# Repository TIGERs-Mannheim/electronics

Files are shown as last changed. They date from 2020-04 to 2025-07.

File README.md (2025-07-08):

# TIGERs Mannheim Open-Source Electronics

This repository contains electronics for our robots and our base station. There is one folder for each released version.  
Have a look at our [2020 ETDP](https://tigers-mannheim.de/download/tdps/2020_ETDP_TIGERS.pdf) which contains many details about design decisions and lessons learned over the last 10 years.

The following files are present for each release.

### EAGLE
Electronics are designed with [Autodesk EAGLE](https://www.autodesk.com/education/free-software/eagle) which is available for free for students.
This folder contains all schematics (.sch) and board (.brd) files.

### KiCad9
EAGLE files converted to KiCad version 9. Files got only a light cleanup pass.
Note that no PCBs were ever produced using these files. The EAGLE files are still the ground truth.

### PDF
All schematics are also available as PDF files. This makes it easier to view them without a need to install EAGLE.

### CAM
CAM jobs for EAGLE. Used to produce manufacturing data from board files.

### Gerber
Production ready zip packages for all boards. Most PCB production services directly accept gerber files.

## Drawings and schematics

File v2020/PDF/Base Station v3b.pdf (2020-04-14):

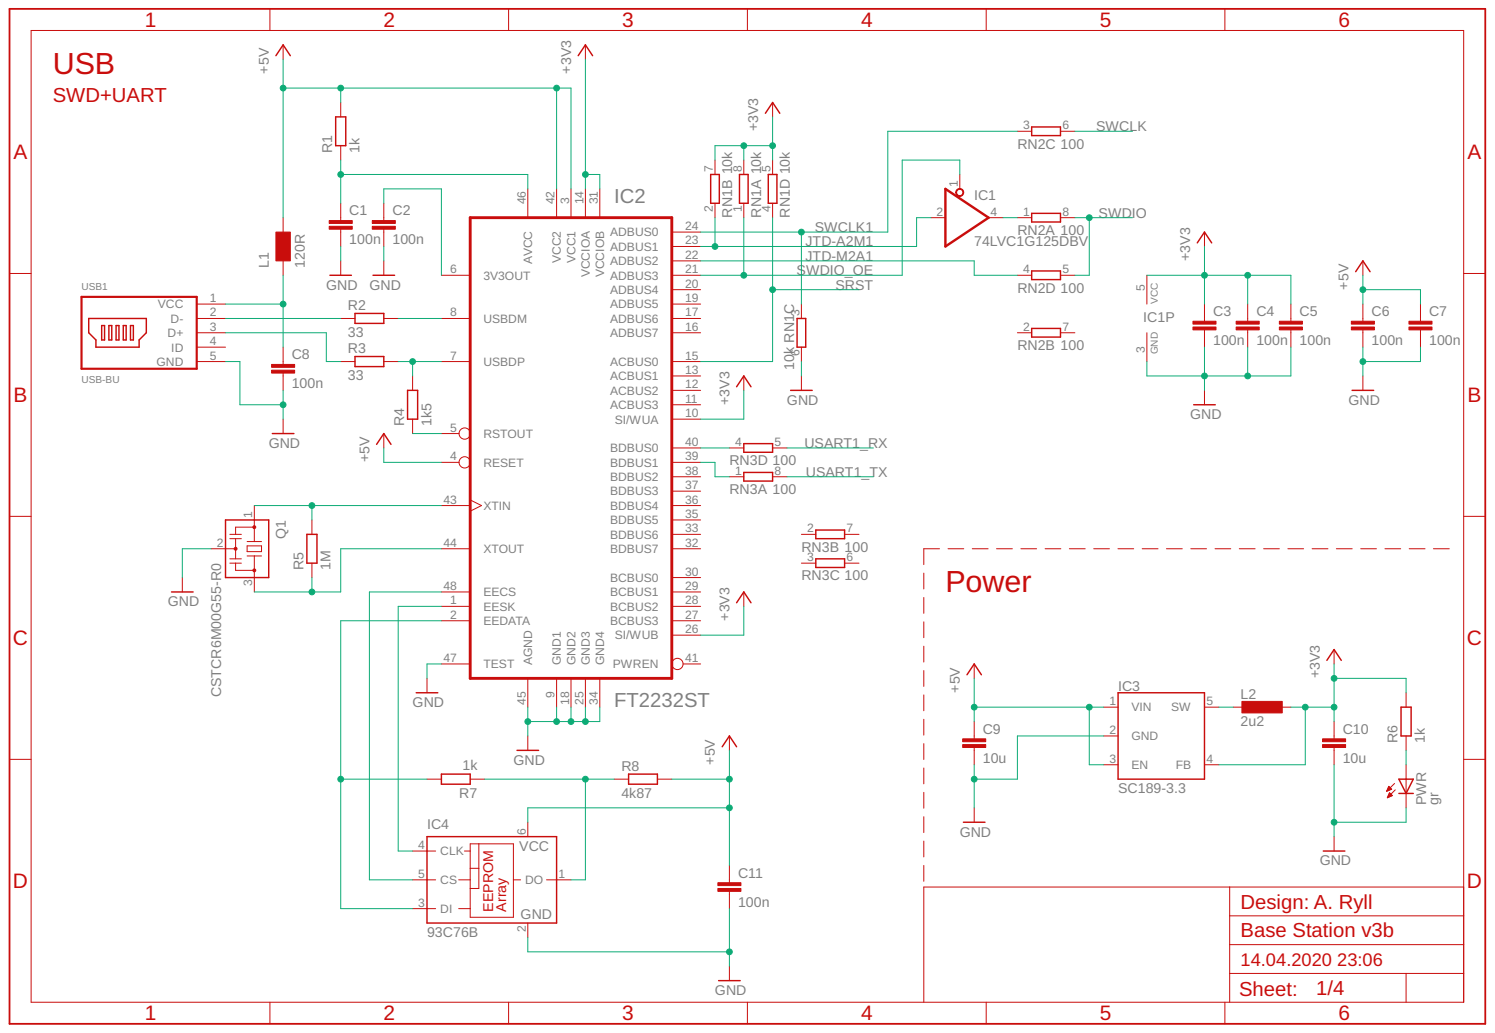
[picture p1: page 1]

23 ADBUS2 | | JTD-M2A1
22 ADBUS3 21 ADBUS4 | SWDIO_OE

JTD-A2M1

4 GND
ID

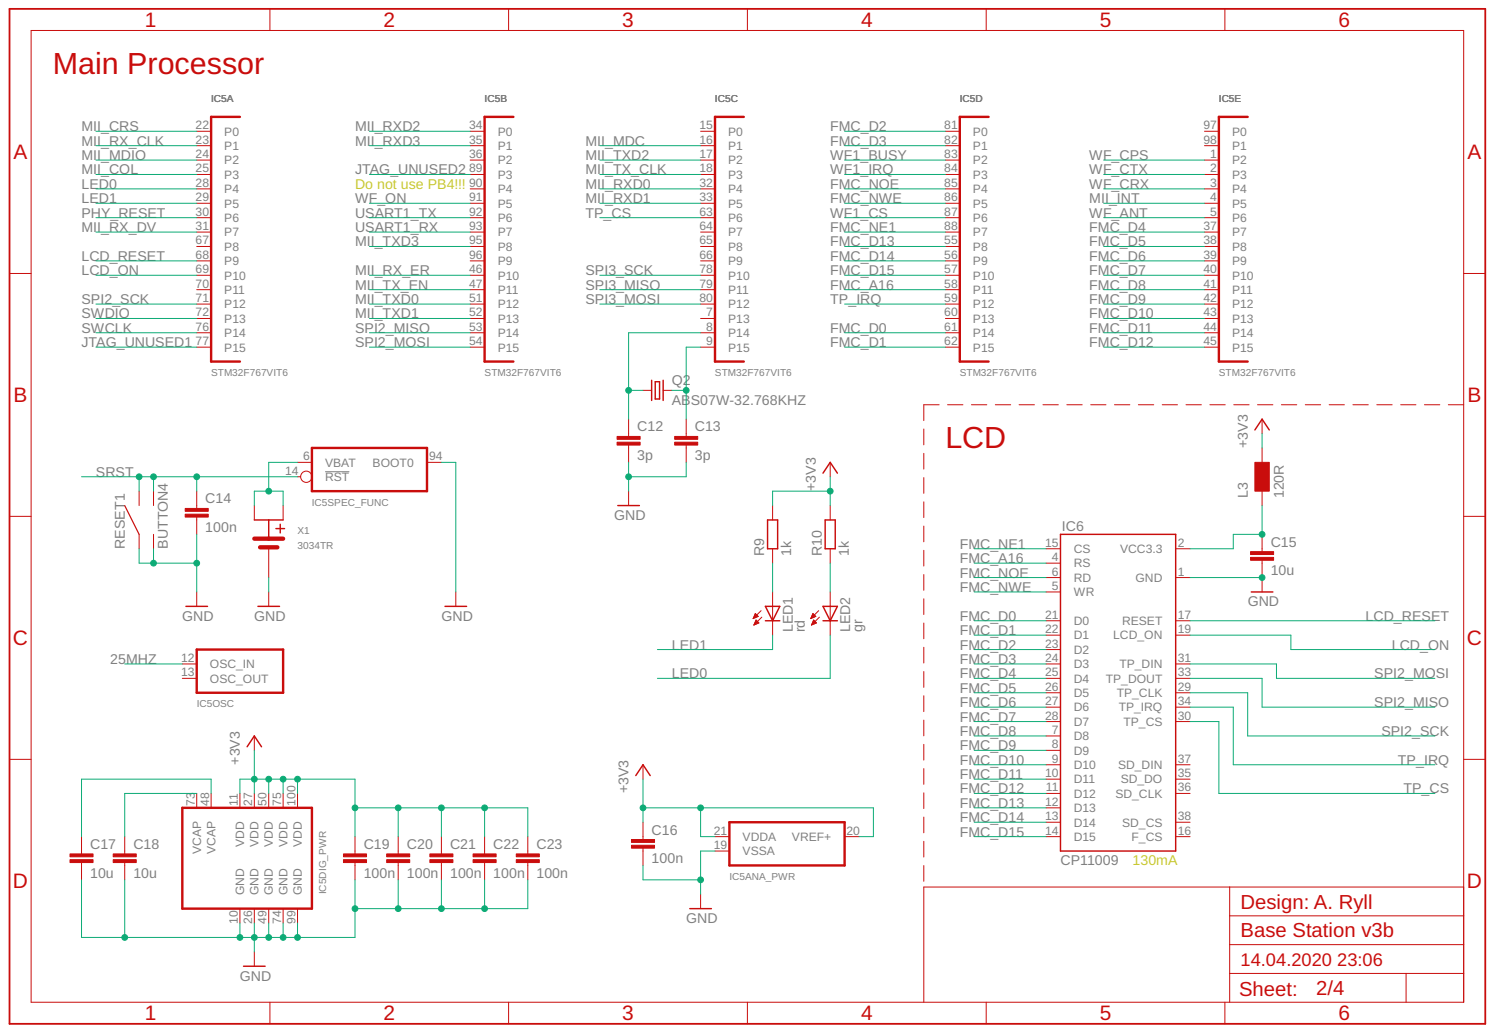
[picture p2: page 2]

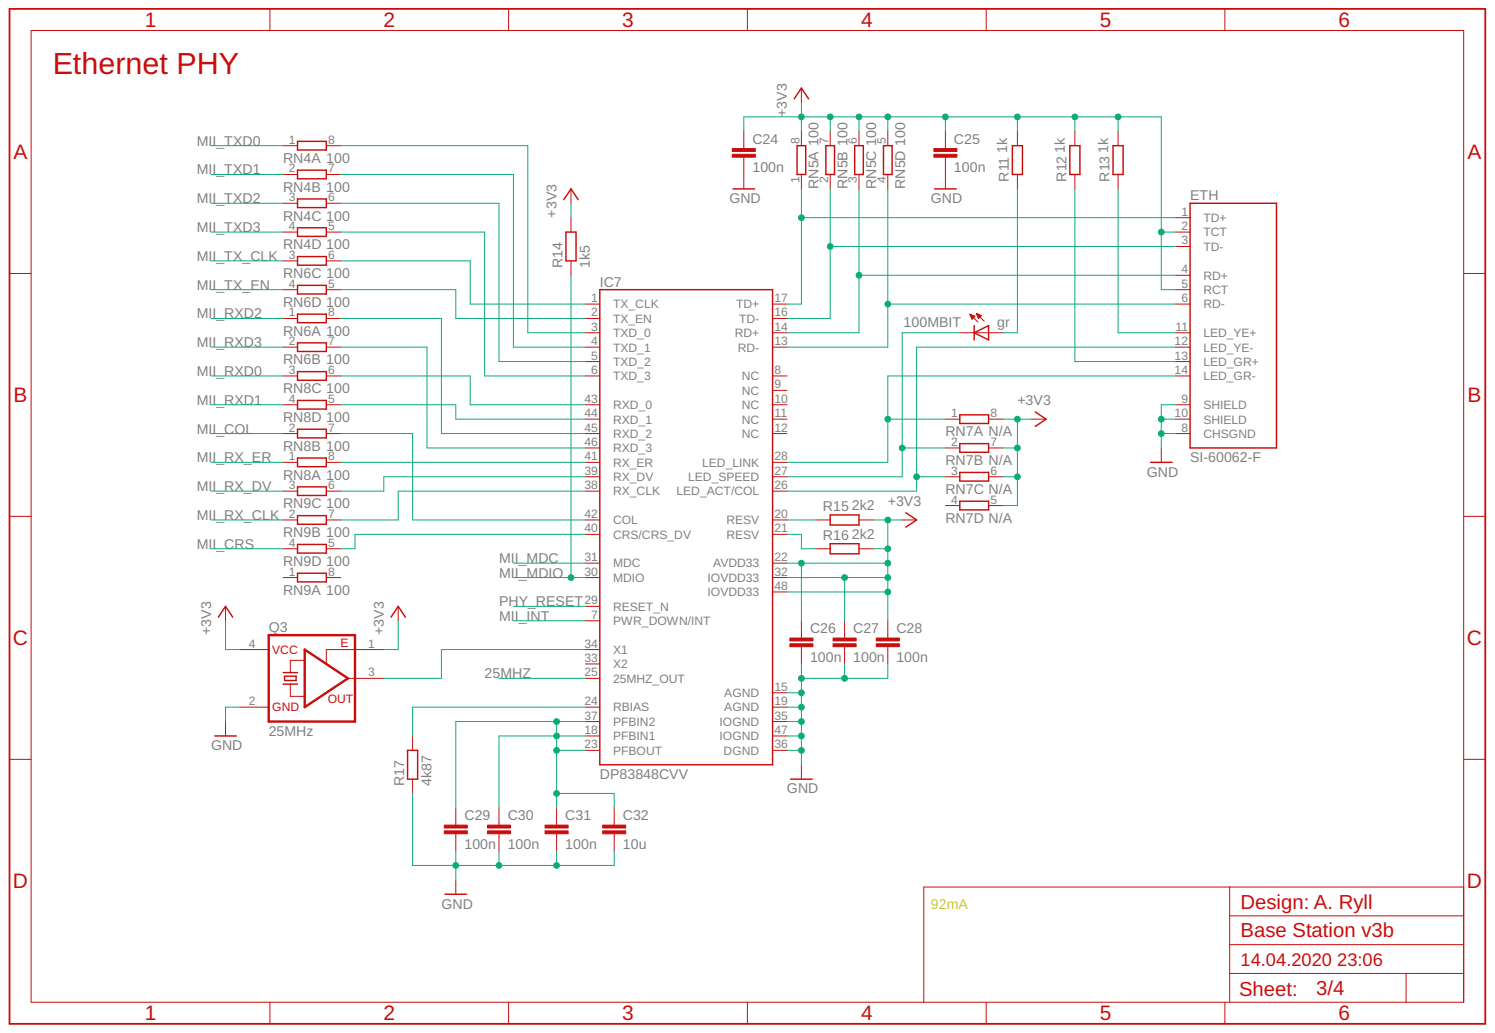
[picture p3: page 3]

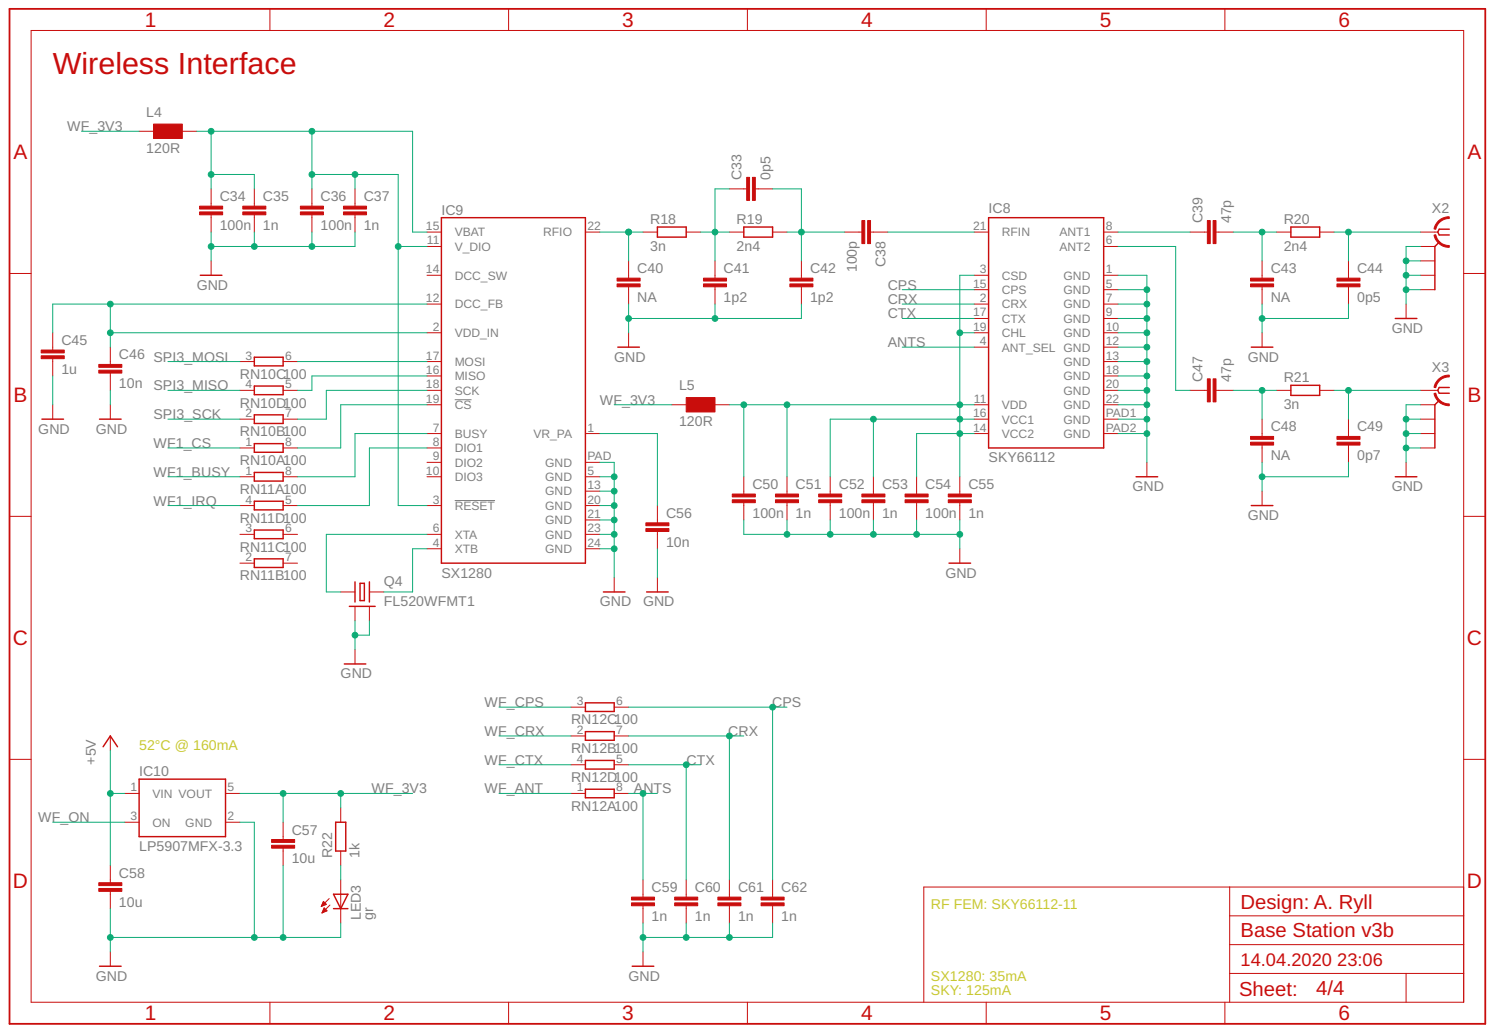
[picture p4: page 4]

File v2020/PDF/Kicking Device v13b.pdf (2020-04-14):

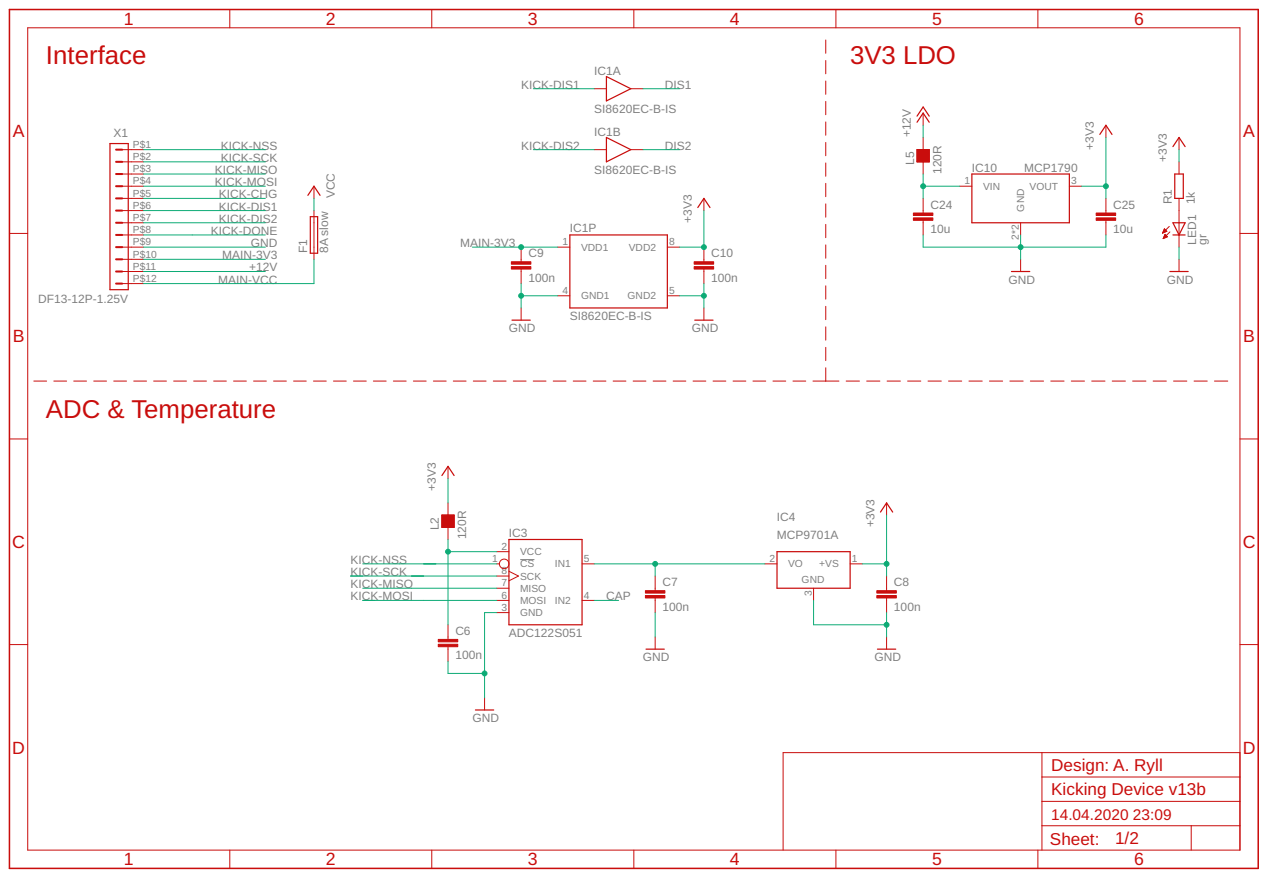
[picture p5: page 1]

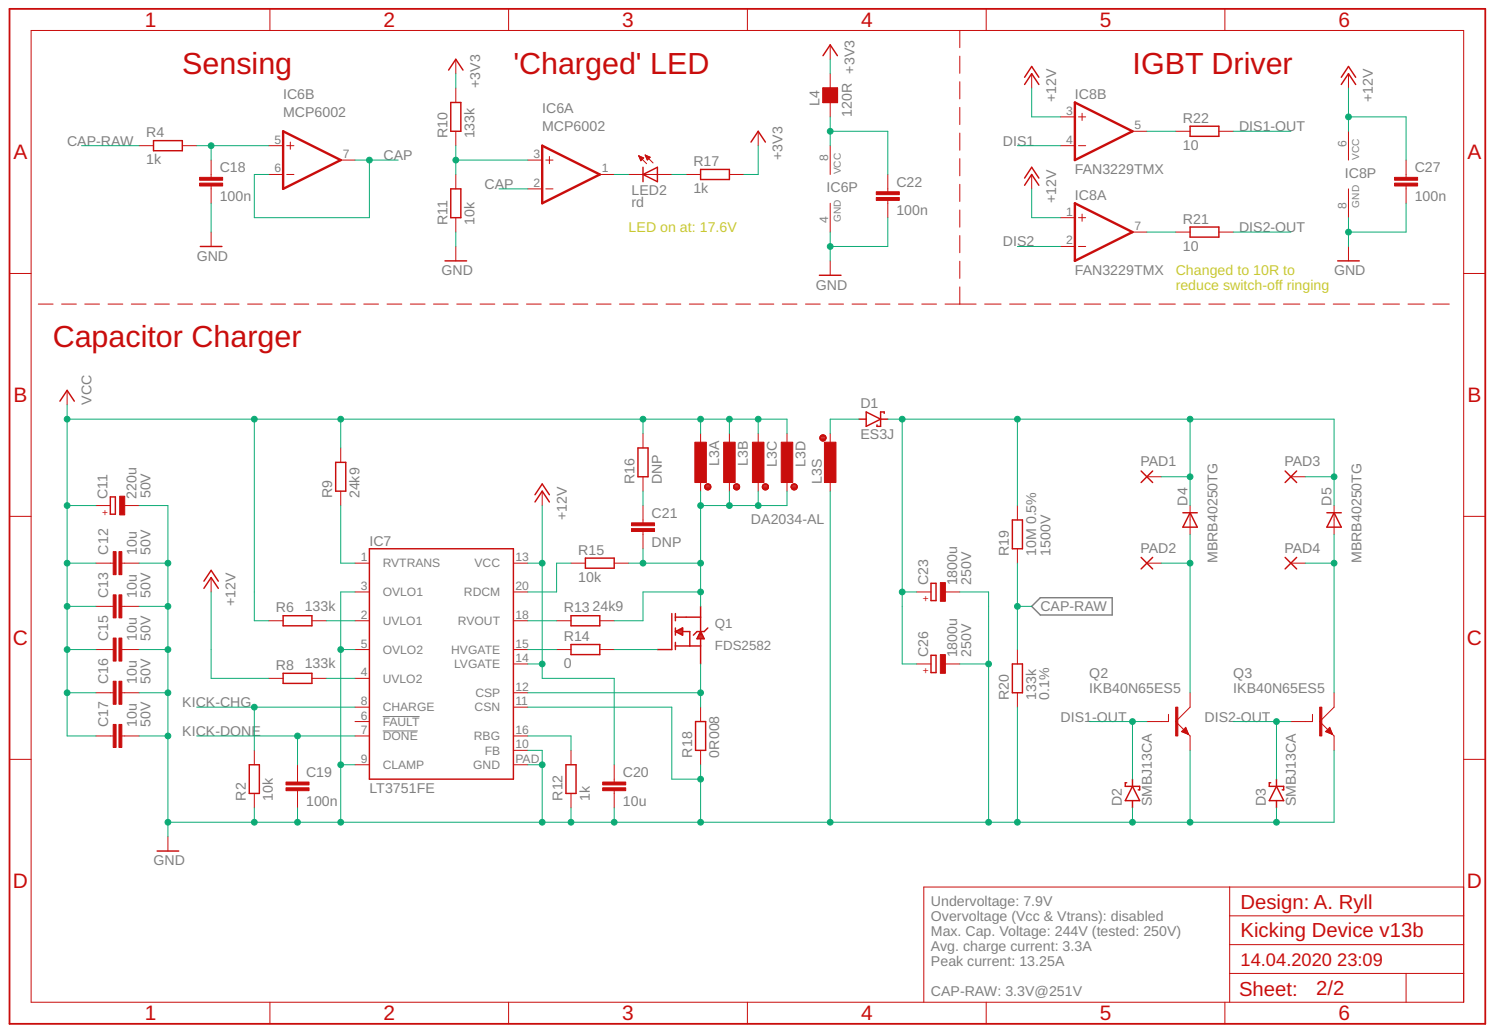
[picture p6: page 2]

Changed to 10R to
reduce switch-off ringing

Undervoltage: 7.9V
Overvoltage (Vcc & Vtrans): disabled
Max. Cap. Voltage: 244V (tested: 250V)
Avg. charge current: 3.3A
Peak current: 13.25A

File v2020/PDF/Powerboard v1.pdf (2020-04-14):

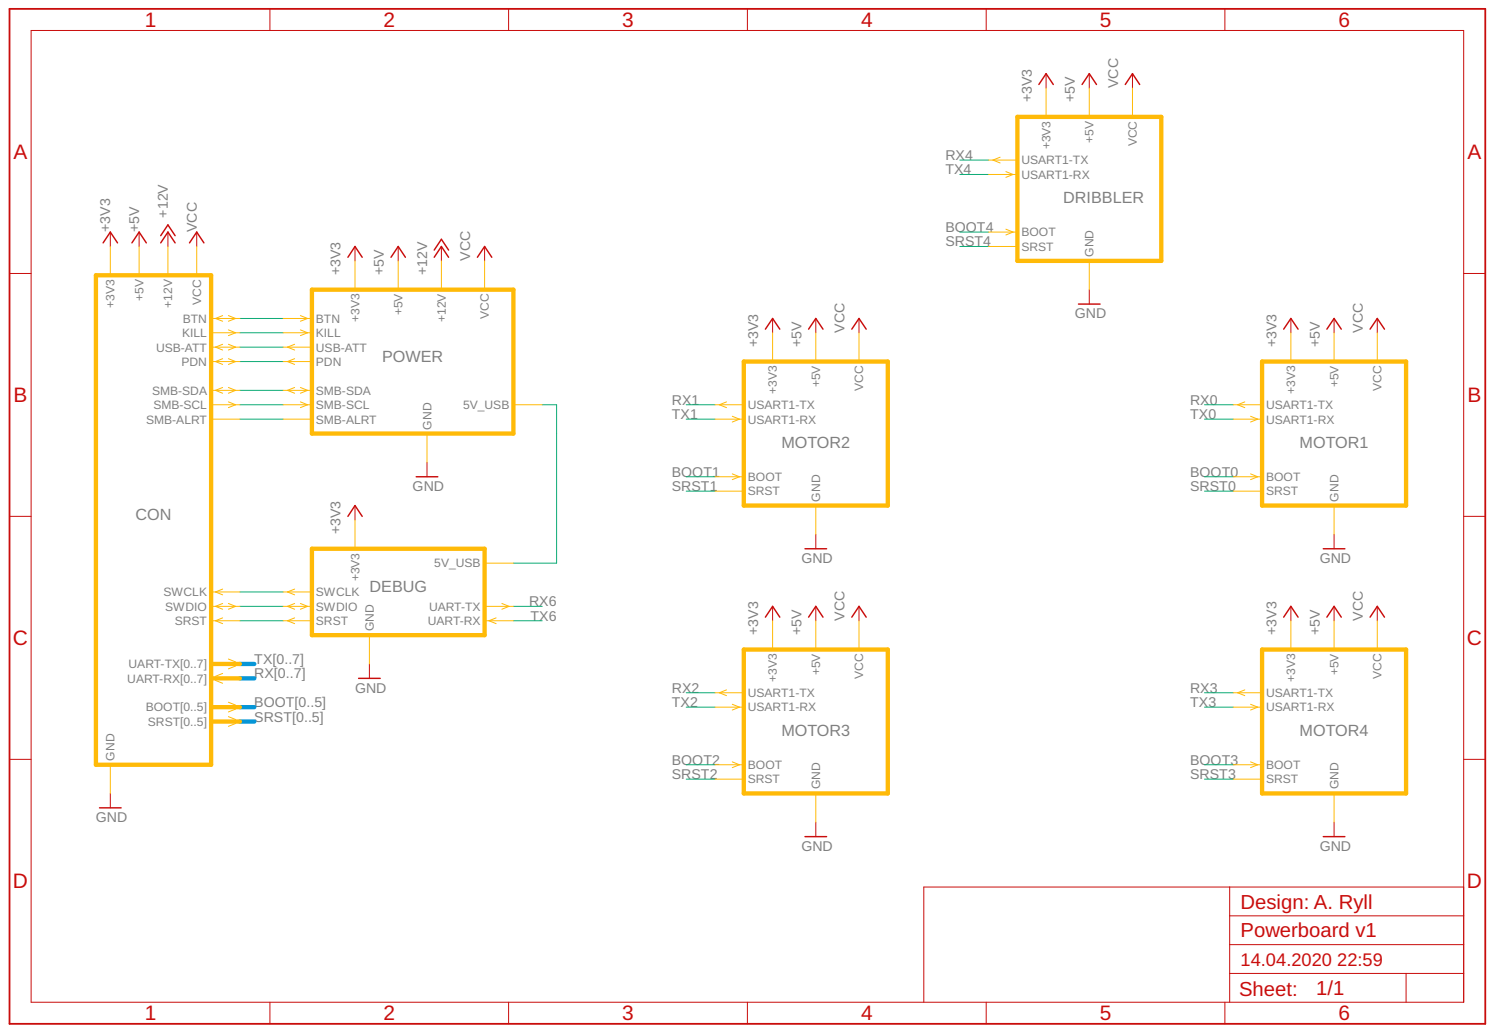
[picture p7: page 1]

+5V GND GND +3V3 +12VVCC GND +3V3 GND GND +3V3 +5VVCC GND +3V3 +5VVCC VCC +5V +3V3 GND +3V3 +5VVCC VCC +5V +3V3 GND +5V +3V3 +12V VCC POWER SMB-SCL SMB-SDA USB-ATT PDN KILL 5V_USB +3V3 +5V +12V VCC GND SMB-ALRT BTN DEBUG 5V_USB UART-TX SRST UART-RX +3V3 GN SWDIO D SWCLK MOTOR1 USART1-TX USART1-RX BOOT+3V3 +5V GND VCC SRST MOTOR2 USART1-TX USART1-RX BOOT+3V3 +5V GND VCC SRST CONSMB-SCL SMB-SDA SWCLK SWDIO KILL SRST +5V GND BOOT[0..5] SRST[0..5] UART-TX[0..7] UART-RX[0..7] SMB-ALRT BTN PDN USB-ATT +12V VCC +3V3 MOTOR3 USART1-TX USART1-RX BOOT+3V3 +5V GND VCC SRST MOTOR4 USART1-TX USART1-RX BOOT+3V3 +5V GND VCC SRST DRIBBLER +3V3 +5V VCC USART1-TX USART1-RX BOOT SRST GND SRST[0..5] BOOT[0..5] TX[0..7] RX[0..7] RX0 TX0 RX3 TX3 RX1 TX1 RX2 TX2 RX4 TX4 BOOT1 BOOT0 BOOT2 BOOT3 SRST1 SRST0 SRST2 SRST3 BOOT4 SRST4 RX6 TX6 Design: A. Ryll Sheet: ABCD 1 2 3 4 5 6 ABCD 1 2 3 4 5 6 Powerboard v1 14.04.2020 22:59 1/1

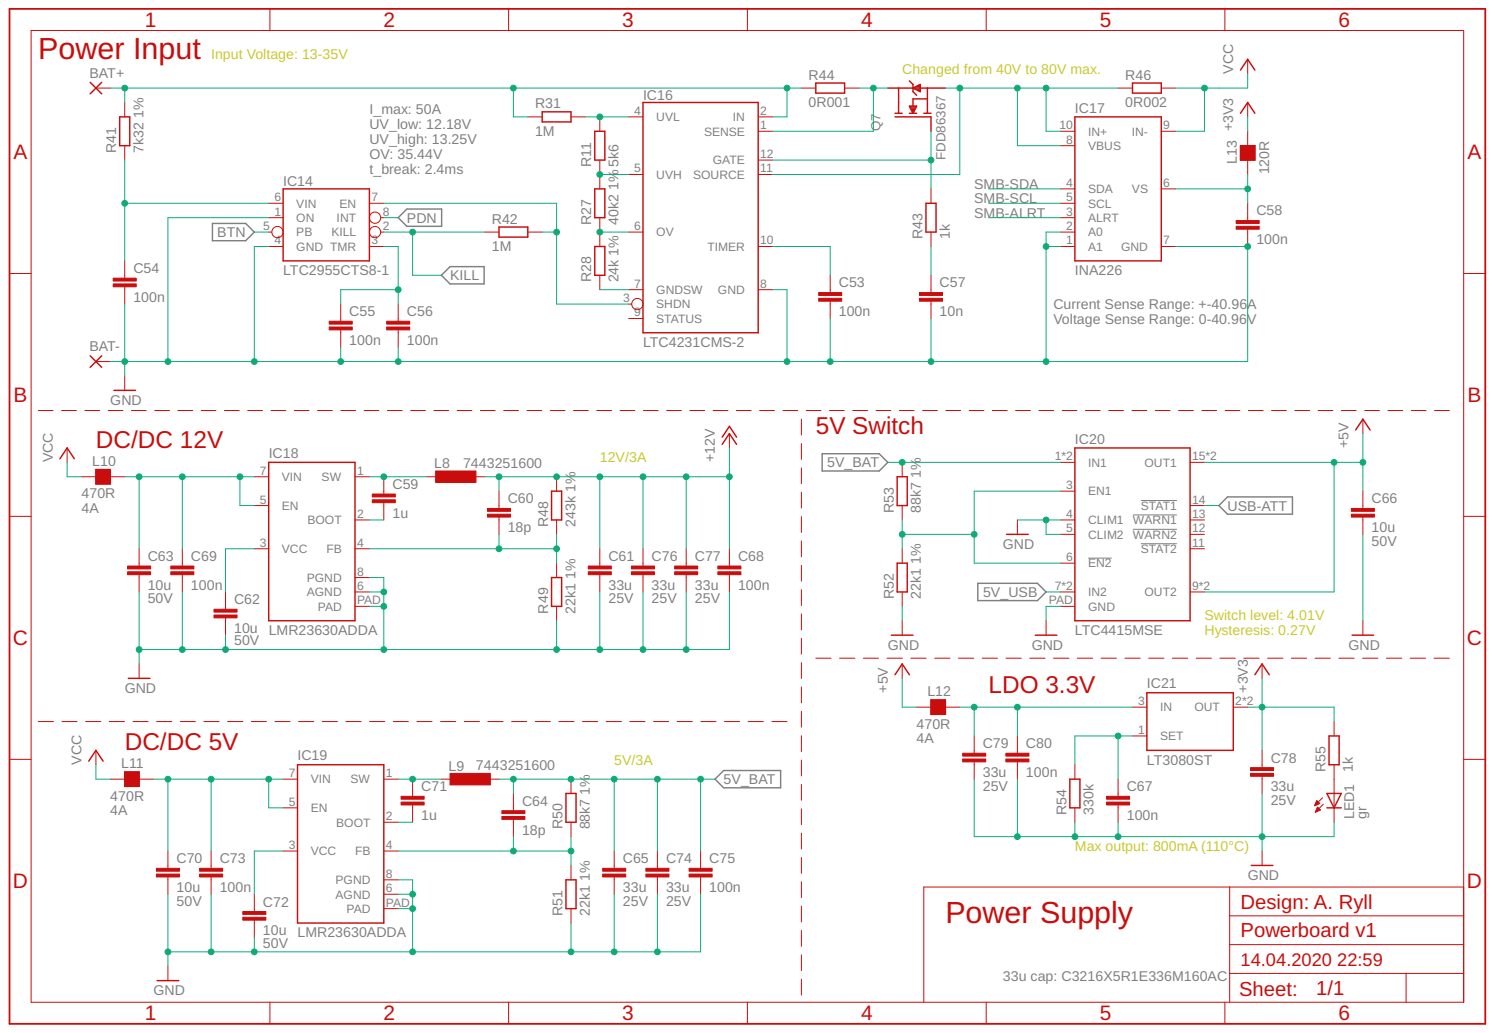
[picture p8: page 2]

Changed from 40V to 80V max.

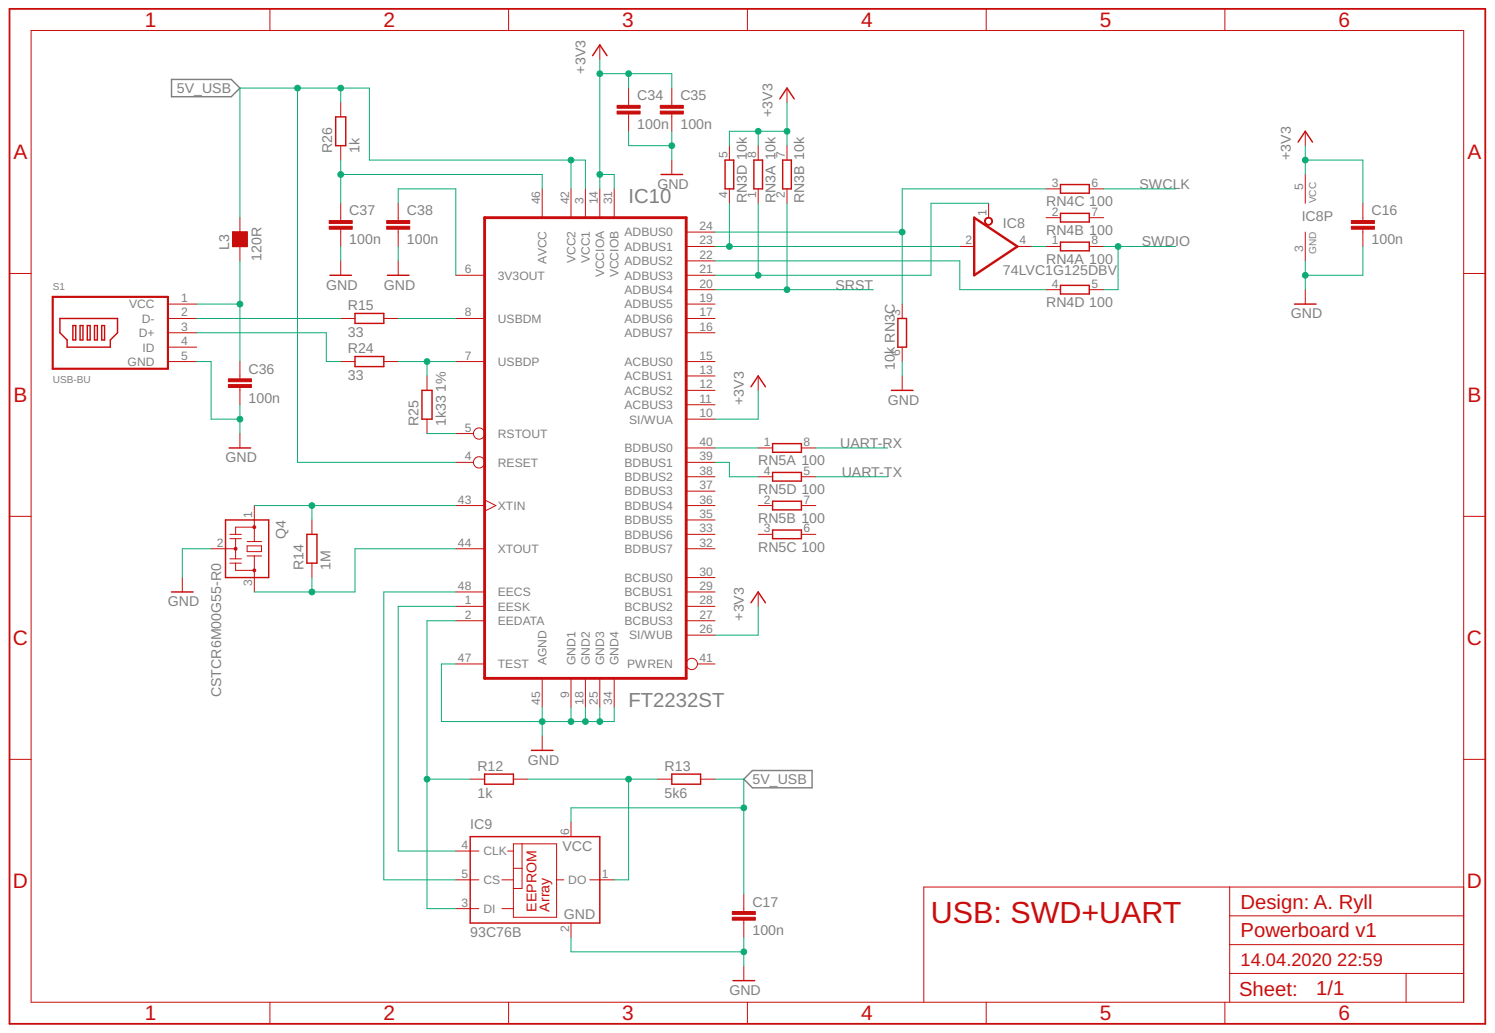
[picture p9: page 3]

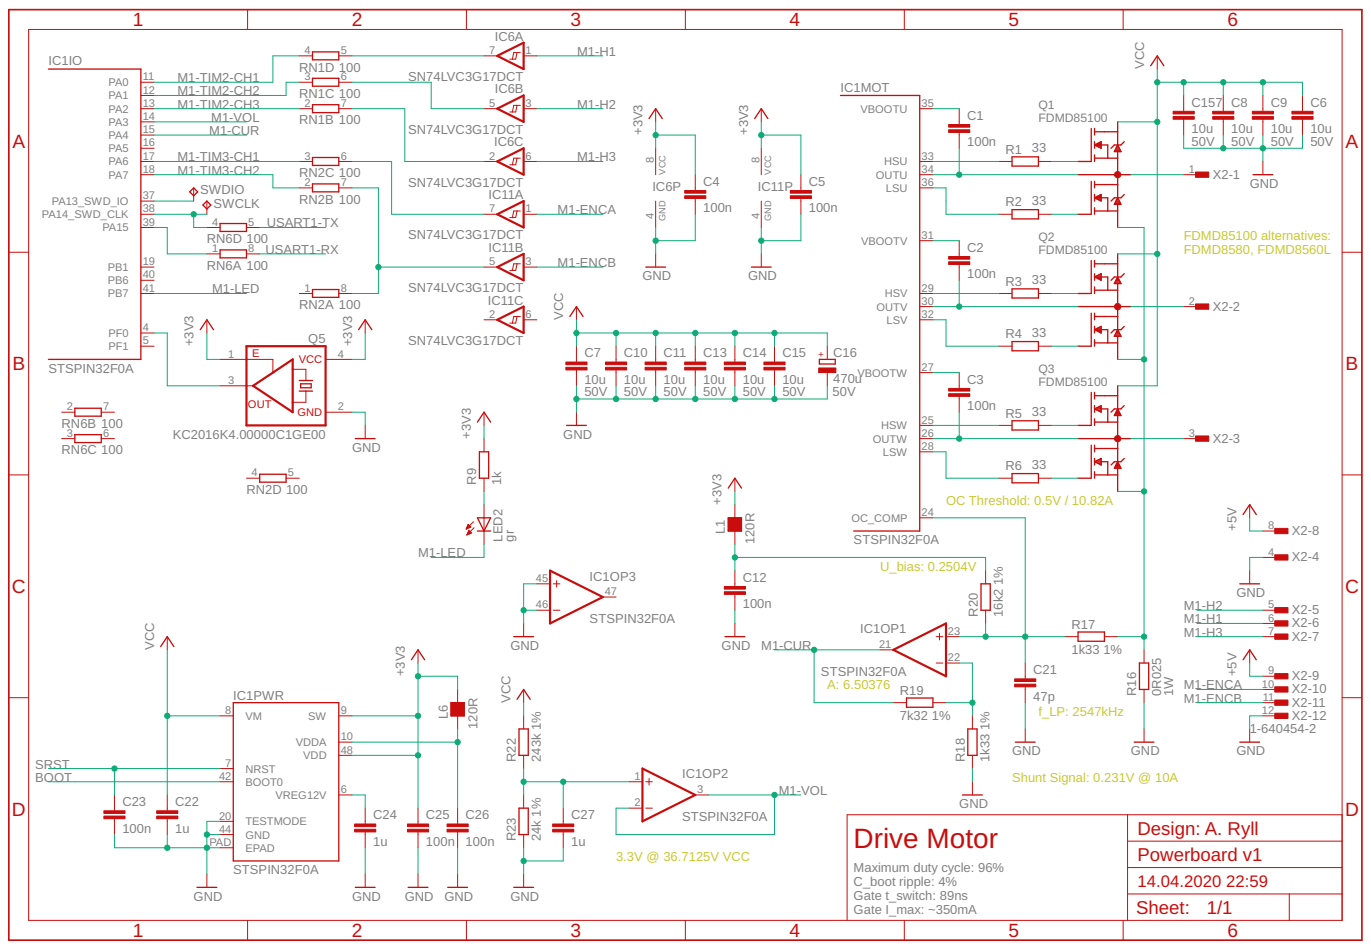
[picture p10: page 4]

Maximum duty cycle: 96% C_boot ripple: 4% Gate t_switch: 89ns Gate I_max: ~350mA | Design: A. Ryll Drive Motor

Sheet: 1/1

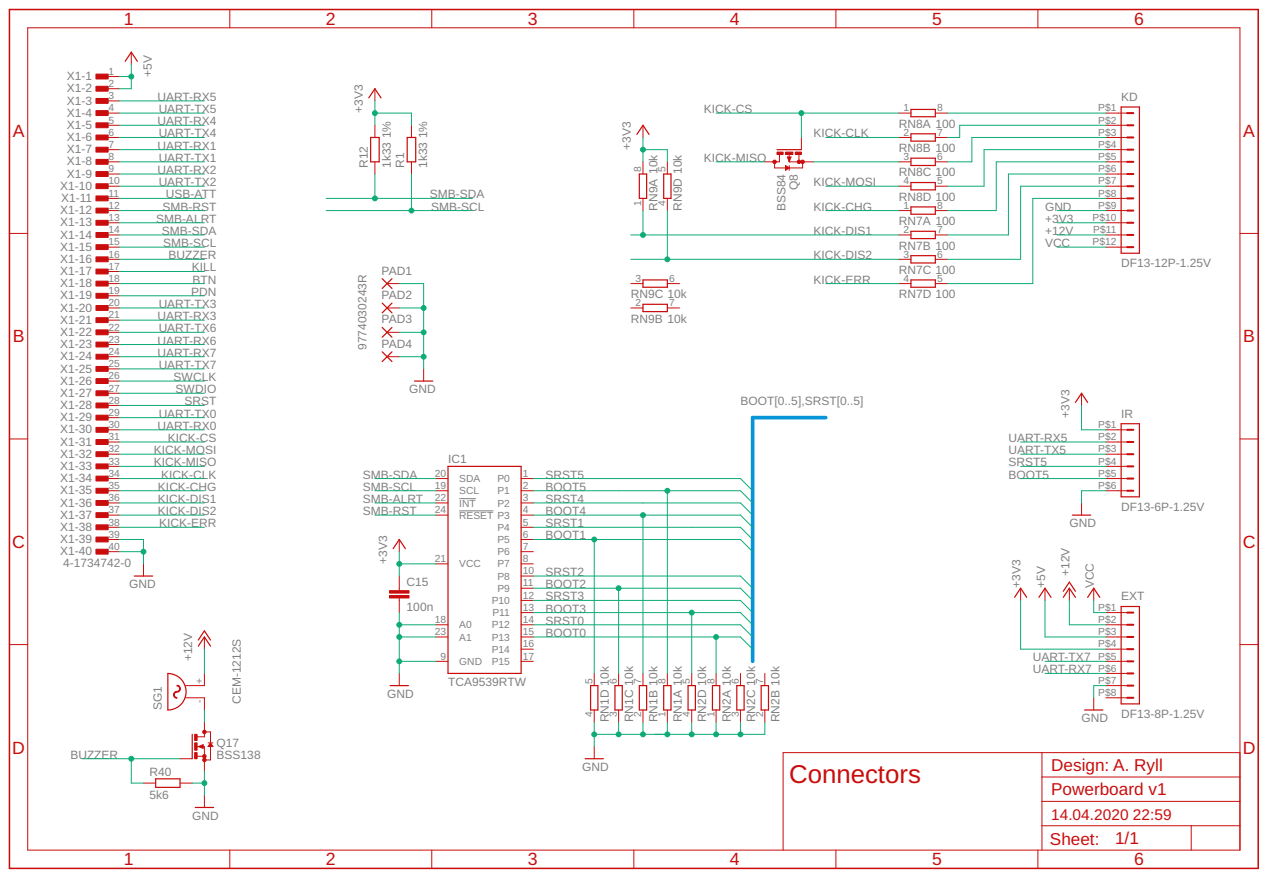
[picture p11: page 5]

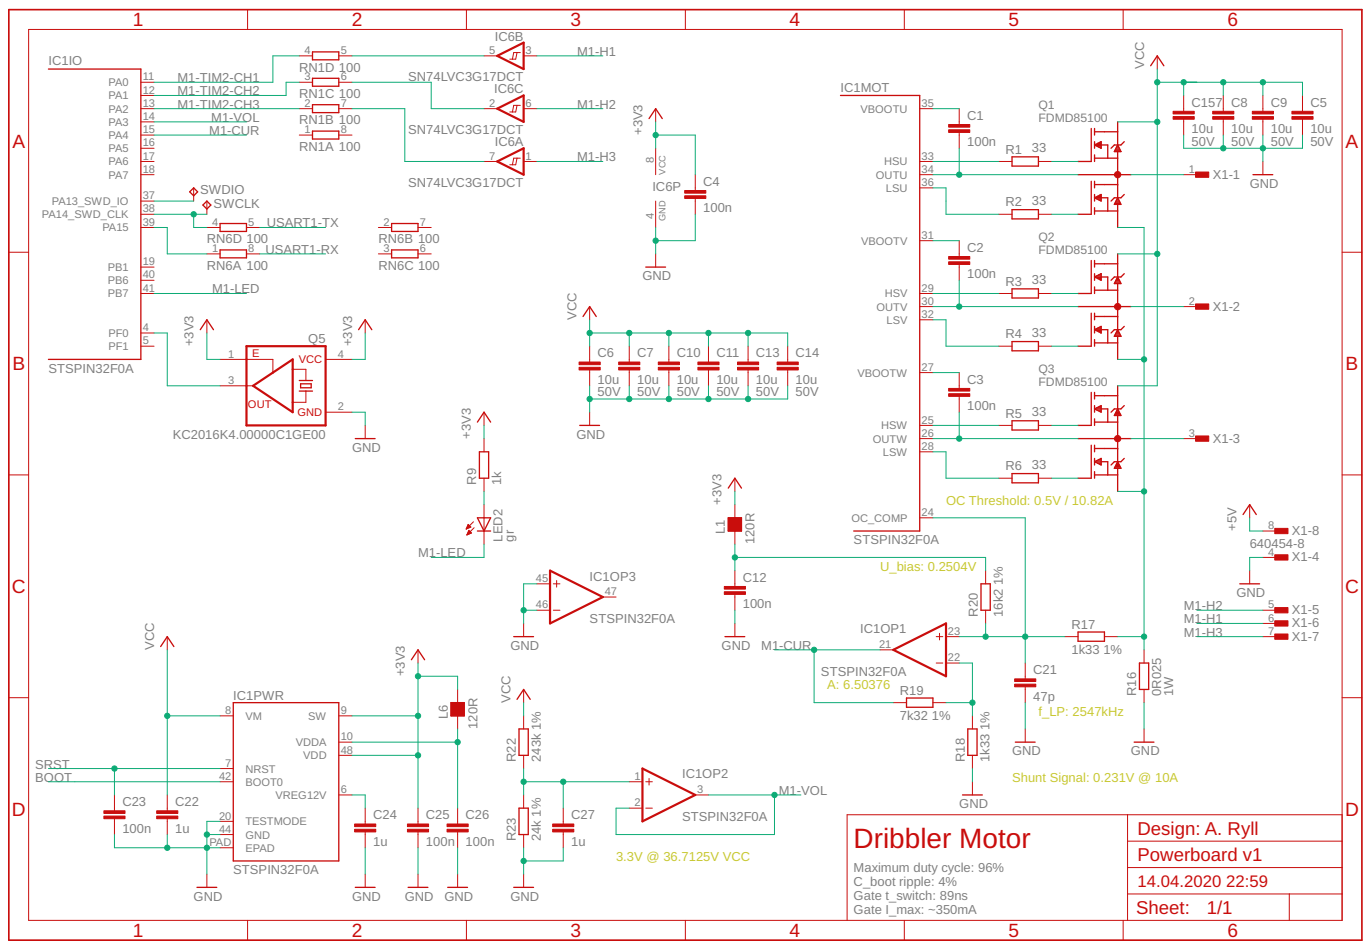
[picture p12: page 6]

Maximum duty cycle: 96% C_boot ripple: 4% Gate t_switch: 89ns Gate I_max: ~350mA | Design: A. Ryll Dribbler Motor

Sheet: 1/1










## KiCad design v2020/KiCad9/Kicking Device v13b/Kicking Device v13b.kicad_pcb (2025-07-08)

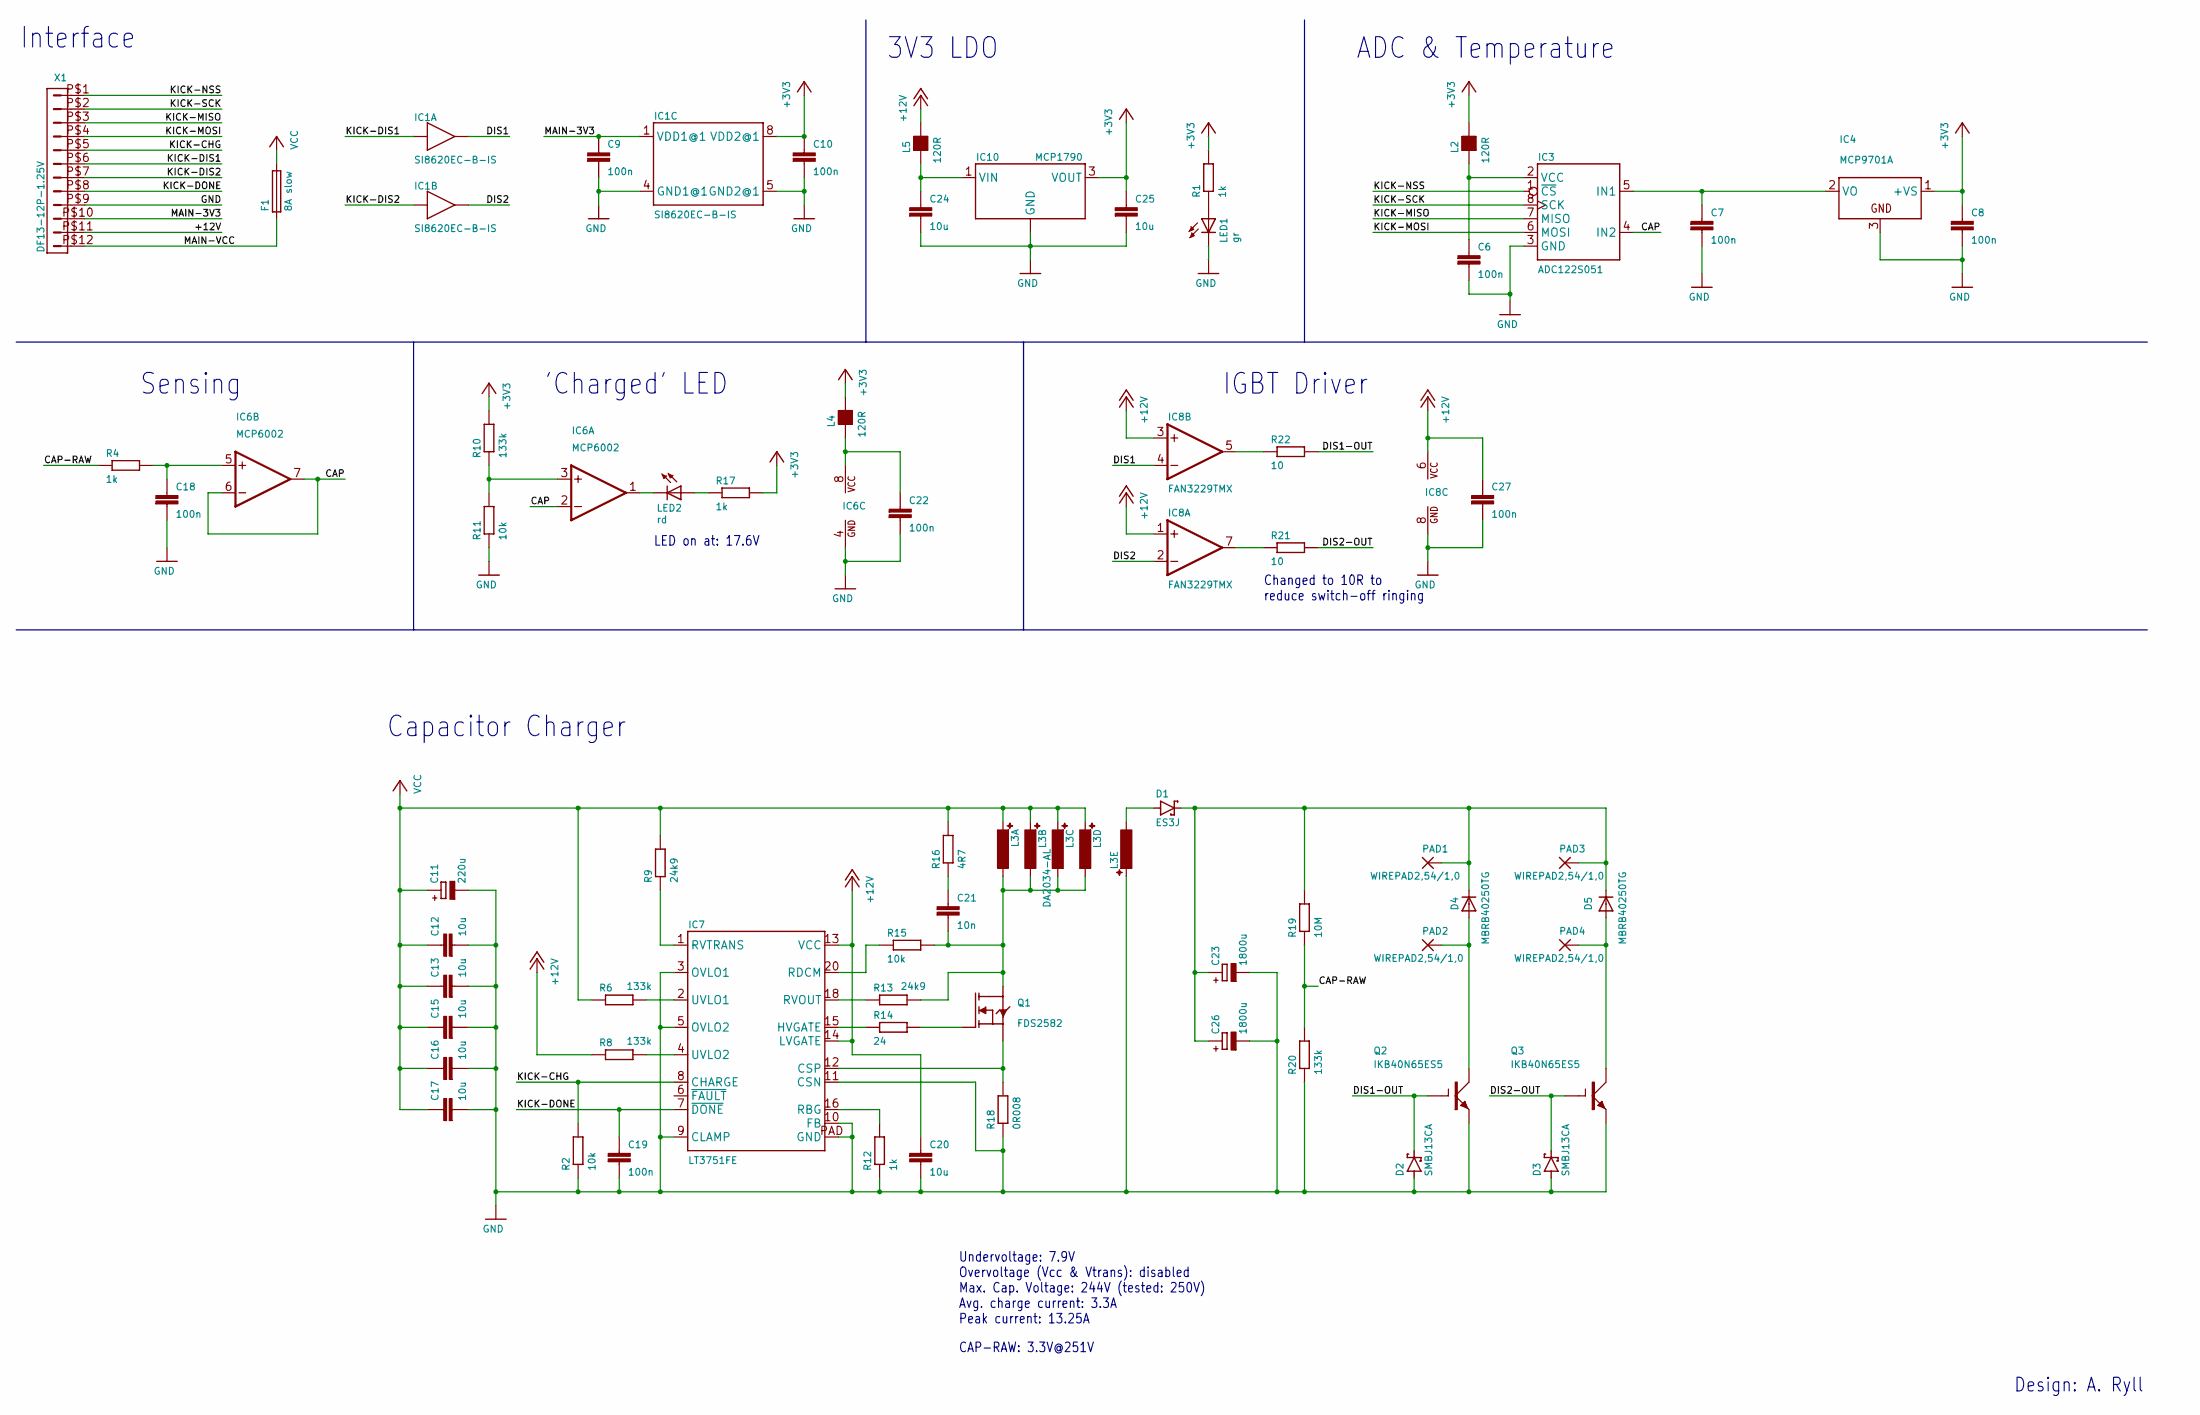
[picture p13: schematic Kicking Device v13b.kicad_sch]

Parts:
C6, C7, C8, C9, C10, C18, C19, C22, C27: 100n; C0603; Digi-Key 1292-1397-1-ND
C11: 220u; PANASONIC_F; Mfg Part # EEEFT1H221AP; Digi-Key PCE5025CT-ND
C12, C13, C15, C16, C17: 10u; C1210; Mfg Part # C3225X5R1H106M250AB; Digi-Key 1276-6736-2-ND
C20, C24, C25: 10u; C0603; Digi-Key 490-12737-1-ND
C21: 10n; C0805
C23, C26: 1800u; EB35D; Digi-Key 493-7224-ND
D1: ES3J; SMC; Digi-Key ES3JCT-ND
D2, D3: SMBJ13CA; SMB; Digi-Key SMBJ13CA-FDICT-ND
D4, D5: MBRB40250TG; D2PAK; Digi-Key MBRB40250TGOS-ND
F1: 8A slow; 1206; Digi-Key 507-1194-1-ND
IC1: SI8620EC-B-IS; SOIC8N; Digi-Key 336-2062-5-ND
IC3: ADC122S051; MSOP8; Digi-Key ADC122S051CIMM/NOPBCT-ND
IC4: MCP9701A; SOT23; Digi-Key MCP9701AT-E/TTCT-ND
IC6: MCP6002; SOIC8N; Digi-Key MCP6002T-I/SNCT-ND
IC7: LT3751FE; TSSOP20P; Digi-Key LT3751EFE#PBF-ND
IC8: FAN3229TMX; SOIC8N; Digi-Key FAN3229TMXCT-ND
IC10: MCP1790; SOT223; Digi-Key MCP1790-3302E/DB-ND
L2, L4, L5: 120R; L0603; Digi-Key 490-1037-1-ND
L3: DA2034-AL; Mfg Part # DA2034-AL
LED1: gr; CHIP-LED0603; Digi-Key 732-4980-1-ND
LED2: rd; CHIP-LED0603; Digi-Key 732-4979-1-ND
PAD1, PAD2, PAD3, PAD4: WIREPAD2,54/1,0; 2,54_1,0
Q1: FDS2582; SOIC8N; Digi-Key FDS2582CT-ND
Q2, Q3: IKB40N65ES5; D2PAK; Digi-Key IKB40N65ES5ATMA1CT-ND
R1, R4, R12, R17: 1k; R0603; Digi-Key 311-1.00KHRCT-ND
R2, R11, R15: 10k; R0603; Digi-Key 311-10.0KHRCT-ND
R6, R8, R10, R20: 133k; R0603; Digi-Key P133KDBCT-ND
R9, R13: 24k9; R0603; Digi-Key P24.9KHCT-ND
R14: 24; R1206
R16: 4R7; R0805; Digi-Key RHM4.7KCT-ND
R18: 0R008; R1206; Digi-Key RHM.008ALCT-ND
R19: 10M; R1206; Digi-Key 541-10MBACT-ND
R21, R22: 10; R1206
X1: DF13-12P-1.25V; DF13C-12P-1.25V; Digi-Key H121957CT-ND

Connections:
+3V3: C8.1, C10.1, C25.1, IC1.8 (VDD2@1), IC4.1 (+VS), IC10.3 (VOUT), L2.2, L4.2, R1.2, R10.2, R17.2
+12V: C20.1, C27.1, IC7.13 (VCC), IC7.14 (LVGATE), IC8.1 (+IN), IC8.3 (+IN), IC8.6 (VCC), L5.2, R8.1, X1.P$11 (11)
/CAP: IC3.4 (IN2), IC6.2 (-IN), IC6.6 (-IN), IC6.7 (OUT)
/CAP-RAW: R4.1, R19.1, R20.2
/DIS1: IC1.7 (OUT), IC8.4 (-IN)
/DIS1-OUT: D2.C, Q2.1 (G), R22.2
/DIS2: IC1.6 (OUT), IC8.2 (-IN)
/DIS2-OUT: D3.C, Q3.1 (G), R21.2
/KICK-CHG: IC7.8 (CHARGE), R2.2, X1.P$5 (5)
/KICK-DIS1: IC1.2 (IN), X1.P$6 (6)
/KICK-DIS2: IC1.3 (IN), X1.P$7 (7)
/KICK-DONE: C19.1, IC7.7 (~DONE), X1.P$8 (8)
/KICK-MISO: IC3.7 (MISO), X1.P$3 (3)
/KICK-MOSI: IC3.6 (MOSI), X1.P$4 (4)
/KICK-NSS: IC3.1 (~CS), X1.P$1 (1)
/KICK-SCK: IC3.8 (SCK), X1.P$2 (2)
/MAIN-3V3: C9.1, IC1.1 (VDD1@1), X1.P$10 (10)
/MAIN-VCC: F1.1, X1.P$12 (12)
GND: C6.2, C7.2, C8.2, C9.2, C10.2, C11.-, C12.2, C13.2, C15.2, C16.2, C17.2, C18.2, C19.2, C20.2, C22.2, C23.-, C24.2, C25.2, C26.-, C27.2, D2.A, D3.A, IC1.4 (GND1@1), IC1.5 (GND2@1), IC3.3 (GND), IC4.3 (GND), IC6.4 (GND), IC7.3 (OVLO1), IC7.5 (OVLO2), IC7.9 (CLAMP), IC7.10 (FB), IC7.11 (CSN), IC7.PAD (GND), IC8.8 (GND), IC10.2 (GND), IC10.4 (GND), L3.12 (2), LED1.C, Q2.3 (E), Q3.3 (E), R2.1, R11.1, R12.1, R18.1, R20.1, X1.P$9 (9)
unnamed: C21.1, R16.1
unnamed: D1.A, L3.1
unnamed: C23.+, C26.+, D1.C, D4.2 (C), D5.2 (C), PAD1.1, PAD3.1, R19.2
unnamed: C7.1, IC3.5 (IN1), IC4.2 (VO)
unnamed: C6.1, IC3.2 (VCC), L2.1
unnamed: IC6.3 (+IN), R10.1, R11.2
unnamed: IC6.1 (OUT), LED2.C
unnamed: C18.1, IC6.5 (+IN), R4.2
unnamed: C22.1, IC6.8 (VCC), L4.1
unnamed: IC7.12 (CSP), Q1.1 (S), Q1.2 (S), Q1.3 (S), R18.2
unnamed: IC7.15 (HVGATE), R14.1
unnamed: IC7.16 (RBG), R12.2
unnamed: IC7.20 (RDCM), R15.1
unnamed: IC7.18 (RVOUT), R13.1
unnamed: IC7.1 (RVTRANS), R9.1
unnamed: IC7.2 (UVLO1), R6.2
unnamed: IC7.4 (UVLO2), R8.2
unnamed: IC8.7 (OUT), R21.1
unnamed: IC8.5 (OUT), R22.1
unnamed: C24.1, IC10.1 (VIN), L5.1
unnamed: C21.2, L3.7 (1), L3.8 (1), L3.9 (1), L3.10 (1), Q1.5 (D), Q1.6 (D), Q1.7 (D), Q1.8 (D), R13.2, R15.2
unnamed: LED1.A, R1.1
unnamed: LED2.A, R17.1
unnamed: D4.1 (A), D4.3 (A), PAD2.1, Q2.2 (C)
unnamed: D5.1 (A), D5.3 (A), PAD4.1, Q3.2 (C)
unnamed: Q1.4 (G), R14.2
VCC: C11.+, C12.1, C13.1, C15.1, C16.1, C17.1, F1.2, L3.3 (2), L3.4 (2), L3.5 (2), L3.6 (2), R6.1, R9.2, R16.2

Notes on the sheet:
Undervoltage: 7.9V Overvoltage (Vcc & Vtrans): disabled Max. Cap. Voltage: 244V (tested: 250V) Avg. charge current: 3.3A Peak current: 13.25A
Capacitor Charger
3V3 LDO
LED on at: 17.6V
Changed to 10R to reduce switch-off ringing
ADC & Temperature
Design: A. Ryll
Sensing
CAP-RAW: 3.3V@251V
Interface
IGBT Driver
'Charged' LED

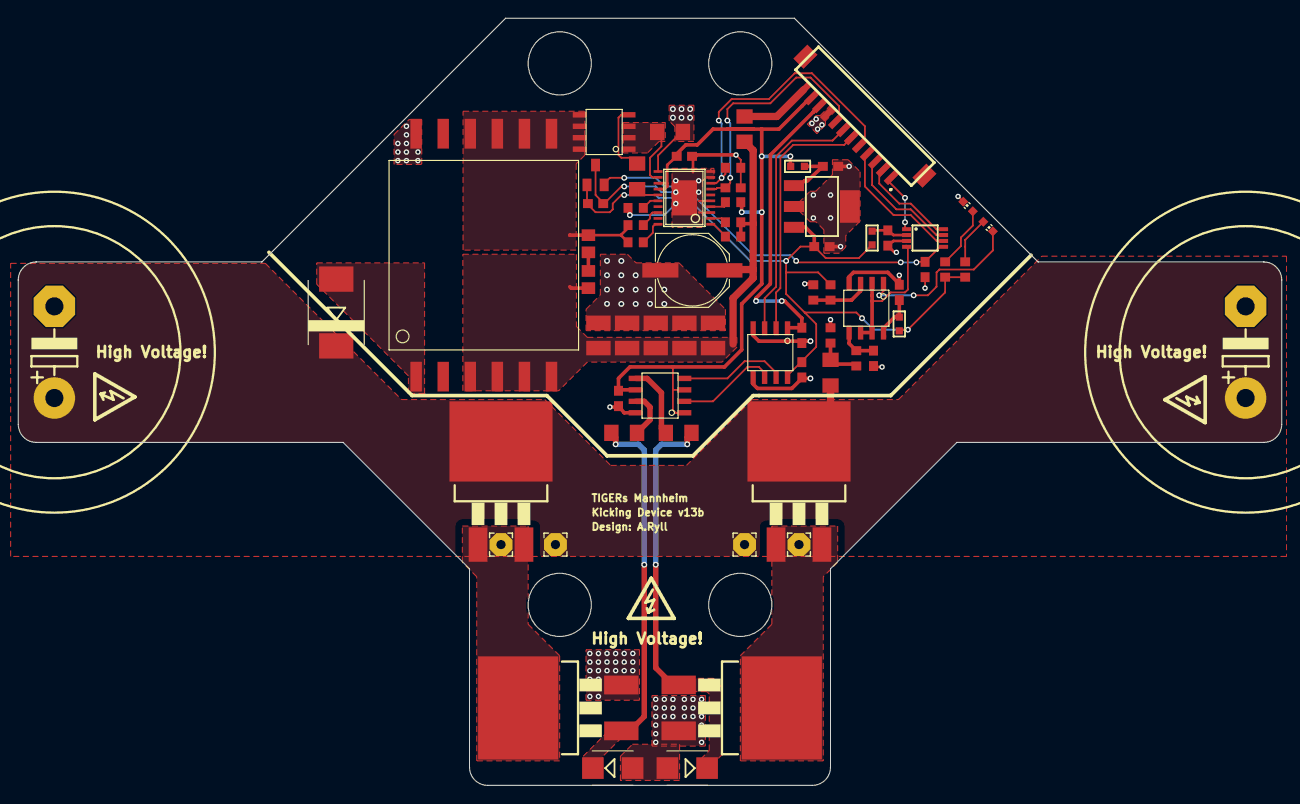
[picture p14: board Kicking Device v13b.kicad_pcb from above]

Board: 2 copper layers, 140.0 x 85.0 mm, 71 parts (0 on the bottom side), 46 nets.

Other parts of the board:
UNK_HOLE_0: dummyfp0
UNK_HOLE_1: dummyfp1
UNK_HOLE_2: dummyfp2
UNK_HOLE_3: dummyfp3

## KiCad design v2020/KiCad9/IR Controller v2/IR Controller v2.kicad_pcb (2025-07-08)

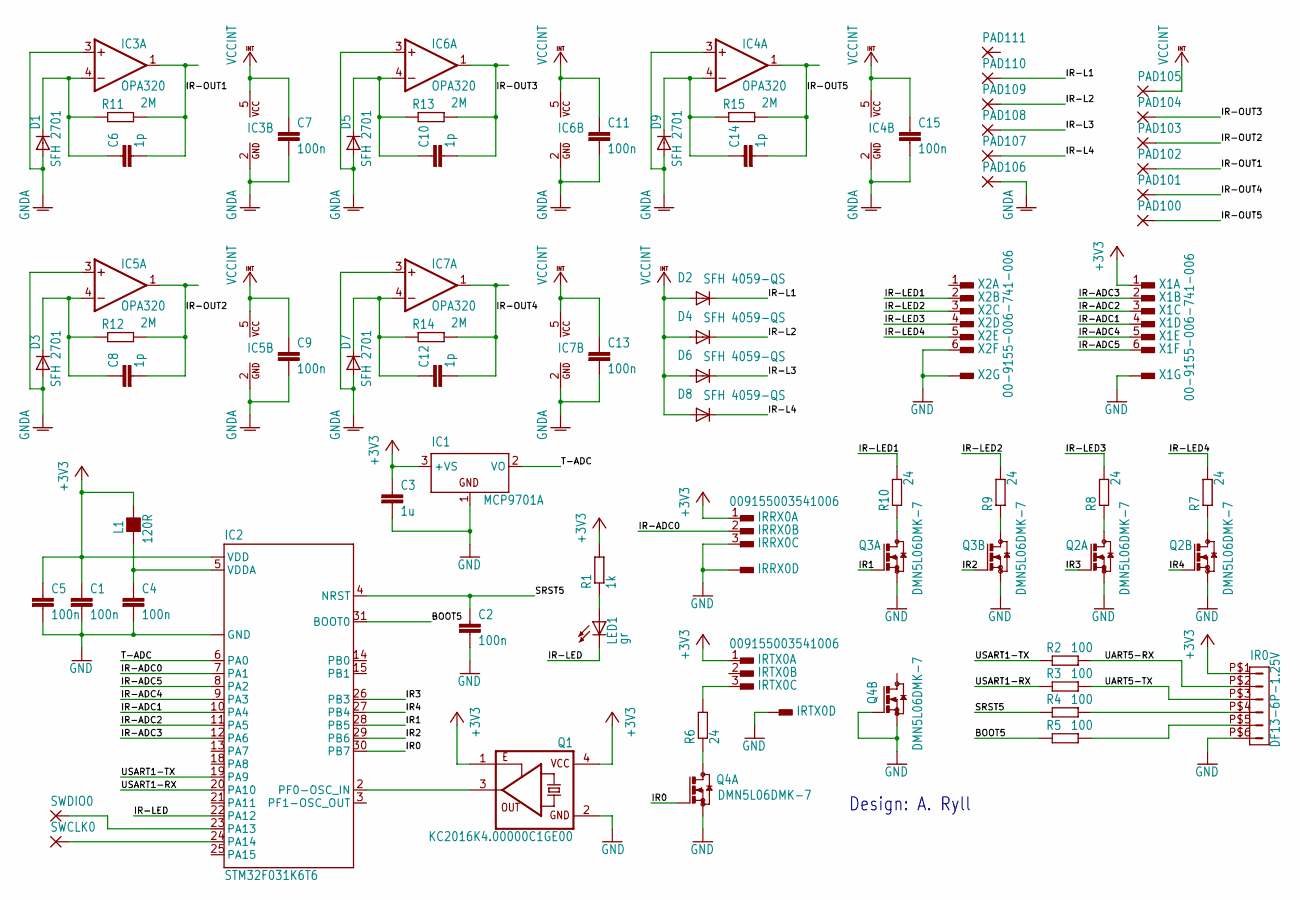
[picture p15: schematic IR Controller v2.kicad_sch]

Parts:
C1, C2, C4, C5, C7, C9, C11, C13, C15: 100n; C0603
C3: 1u; C0603
C6, C8, C10, C12, C14: 1p; C0603
D1, D3, D5, D7, D9: SFH 2701; LED-GULL
D2, D4, D6, D8: SFH 4059-QS; LED-GULL
IC1: MCP9701A; TO92
IC2: STM32F031K6T6; LQFP32-ST
IC3, IC4, IC5, IC6, IC7: OPA320; SOT23-5
IR0: DF13-6P-1.25V; DF13C-6P-1.25V
IRRX0: 009155003541006; AVX-CON3
IRTX0: 009155003541006; AVX-CON3
L1: 120R; L0603
LED1: gr; CHIP-LED0603
PAD100, PAD101, PAD102, PAD103, PAD104, PAD105, PAD106, PAD107, PAD108, PAD109, PAD110, PAD111: WIREPADSMD1,4-3; SMD1,4-3
Q1: KC2016K4.00000C1GE00; OSCI-KC2016
Q2, Q3, Q4: DMN5L06DMK-7; SOT26
R1: 1k; R0603
R2, R3, R4, R5: 100; R0805
R6, R7, R8, R9, R10: 24; R0805
R11, R12, R13, R14, R15: 2M; R0603
SWCLK0: WIREPADSMD1,27-254; SMD1,27-2,54
SWDIO0: WIREPADSMD1,27-254; SMD1,27-2,54
X1, X2: 00-9155-006-741-006; AVX-CON6-2MM

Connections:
+3V3: C1.1, C3.1, C5.1, IC1.3 (+VS), IC2.1 (VDD), IC2.17 (VDD), IR0.P$1 (1), IRRX0.1, IRTX0.1, L1.2, Q1.1 (OE), Q1.4 (VCC), R1.2, X1.1
BOOT5: IC2.31 (BOOT0), R5.1
GND: C1.2, C2.2, C3.2, C4.2, C5.2, IC1.1 (GND), IC2.16 (GND), IC2.32 (GND), IR0.P$6 (6), IRRX0.3, IRRX0.S1, IRRX0.S2, IRTX0.S1, IRTX0.S2, Q1.2 (GND), Q2.1 (S), Q2.4 (S), Q3.1 (S), Q3.4 (S), Q4.1 (S), Q4.2 (G), Q4.4 (S), X1.S1, X1.S2, X2.6, X2.S1, X2.S2
GNDA: C7.2, C9.2, C11.2, C13.2, C15.2, D1.A, D3.A, D5.A, D7.A, D9.A, IC3.2 (GND), IC3.3 (+IN), IC4.2 (GND), IC4.3 (+IN), IC5.2 (GND), IC5.3 (+IN), IC6.2 (GND), IC6.3 (+IN), IC7.2 (GND), IC7.3 (+IN), PAD106.1
IR0: IC2.30 (PB7), Q4.5 (G)
IR1: IC2.28 (PB5), Q3.5 (G)
IR2: IC2.29 (PB6), Q3.2 (G)
IR3: IC2.26 (PB3), Q2.5 (G)
IR4: IC2.27 (PB4), Q2.2 (G)
IR-ADC0: IC2.7 (PA1), IRRX0.2
IR-ADC1: IC2.10 (PA4), X1.4
IR-ADC2: IC2.11 (PA5), X1.3
IR-ADC3: IC2.12 (PA6), X1.2
IR-ADC4: IC2.9 (PA3), X1.5
IR-ADC5: IC2.8 (PA2), X1.6
IR-L1: D2.C, PAD110.1
IR-L2: D4.C, PAD109.1
IR-L3: D6.C, PAD108.1
IR-L4: D8.C, PAD107.1
IR-LED: IC2.22 (PA12), LED1.C
IR-LED1: R10.2, X2.2
IR-LED2: R9.2, X2.3
IR-LED3: R8.2, X2.4
IR-LED4: R7.2, X2.5
IR-OUT1: C6.2, IC3.1 (OUT), PAD102.1, R11.2
IR-OUT2: C8.2, IC5.1 (OUT), PAD103.1, R12.2
IR-OUT3: C10.2, IC6.1 (OUT), PAD104.1, R13.2
IR-OUT4: C12.2, IC7.1 (OUT), PAD101.1, R14.2
IR-OUT5: C14.2, IC4.1 (OUT), PAD100.1, R15.2
unnamed: IR0.P$4 (4), R4.2
unnamed: IC2.23 (PA13), SWDIO0.1
unnamed: IR0.P$5 (5), R5.2
unnamed: IC2.24 (PA14), SWCLK0.1
unnamed: C14.1, D9.C, IC4.4 (-IN), R15.1
unnamed: C10.1, D5.C, IC6.4 (-IN), R13.1
unnamed: C8.1, D3.C, IC5.4 (-IN), R12.1
unnamed: Q3.3 (D), R10.1
unnamed: C6.1, D1.C, IC3.4 (-IN), R11.1
unnamed: IC2.2 (PF0-OSC_IN), Q1.3 (FO)
unnamed: C4.1, IC2.5 (VDDA), L1.1
unnamed: IRTX0.3, R6.2
unnamed: C12.1, D7.C, IC7.4 (-IN), R14.1
unnamed: Q4.3 (D), R6.1
unnamed: Q3.6 (D), R9.1
unnamed: Q2.3 (D), R8.1
unnamed: Q2.6 (D), R7.1
unnamed: LED1.A, R1.1
SRST5: C2.1, IC2.4 (NRST), R4.1
T-ADC: IC1.2 (VO), IC2.6 (PA0)
UART5-RX: IR0.P$2 (2), R2.2
UART5-TX: IR0.P$3 (3), R3.2
USART1-RX: IC2.20 (PA10), R3.1
USART1-TX: IC2.19 (PA9), R2.1
VCCINT: C7.1, C9.1, C11.1, C13.1, C15.1, D2.A, D4.A, D6.A, D8.A, IC3.5 (VCC), IC4.5 (VCC), IC5.5 (VCC), IC6.5 (VCC), IC7.5 (VCC), PAD105.1

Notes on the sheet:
Design: A. Ryll

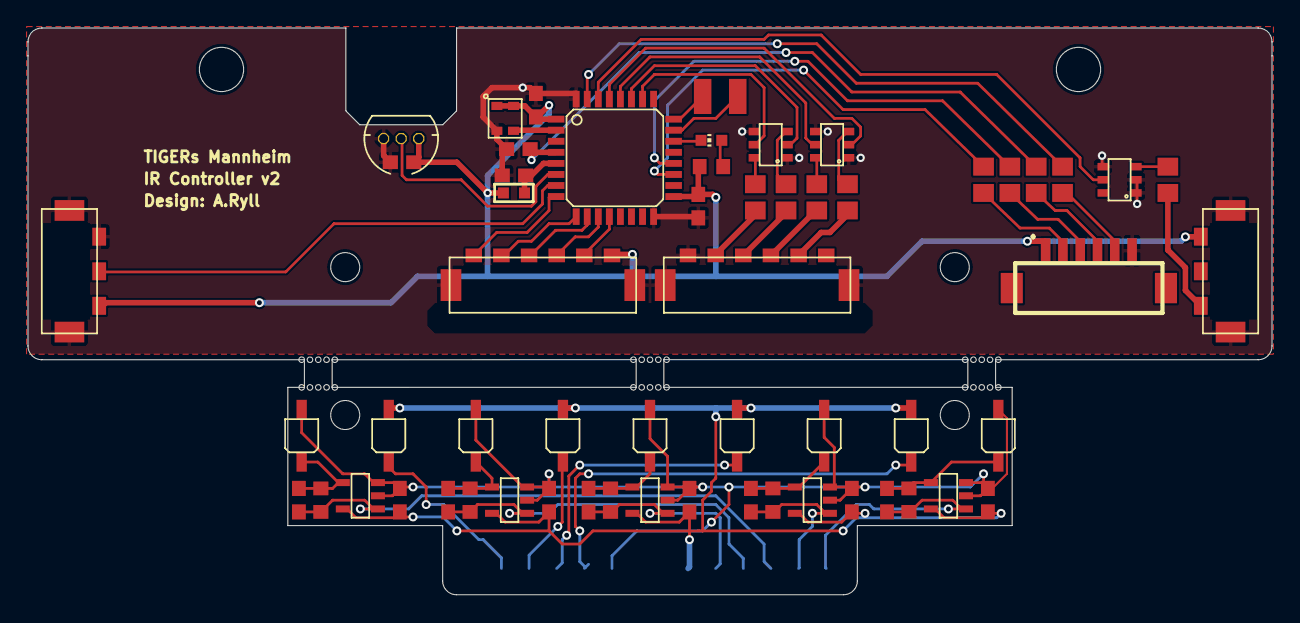
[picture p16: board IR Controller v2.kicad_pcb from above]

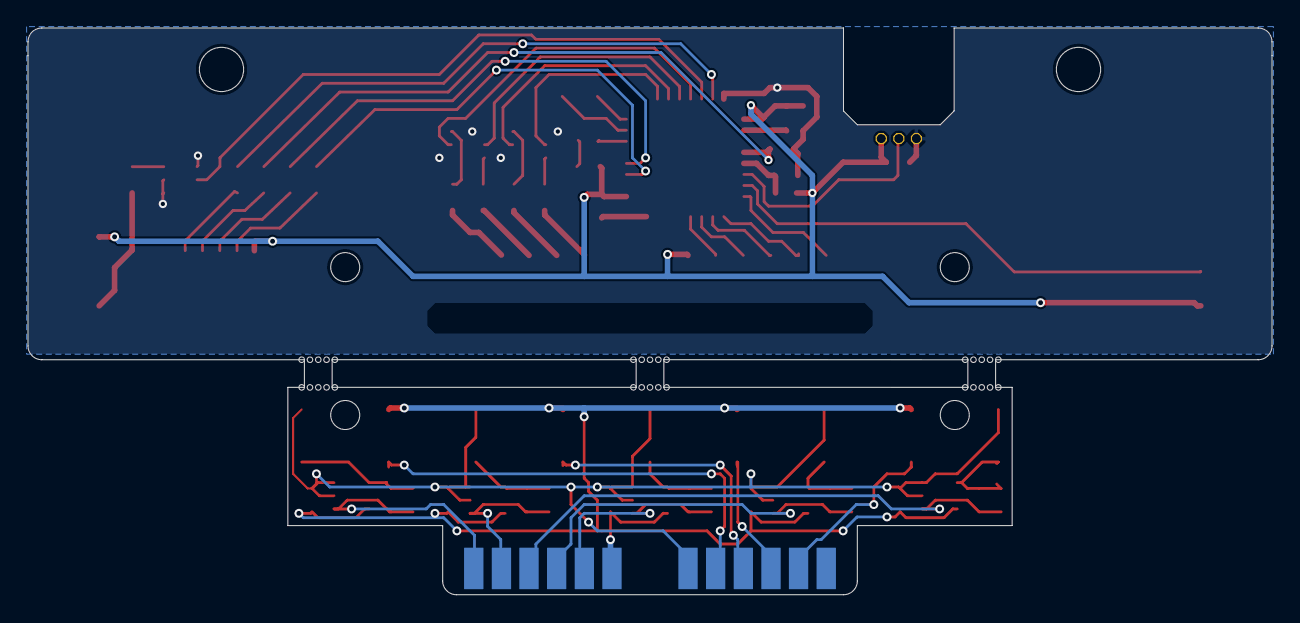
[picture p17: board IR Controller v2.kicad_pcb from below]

Board: 2 copper layers, 90.0 x 41.0 mm, 107 parts (12 on the bottom side), 54 nets.

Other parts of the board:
UNK_HOLE_0: dummyfp0
UNK_HOLE_1: dummyfp1
UNK_HOLE_2: dummyfp2
UNK_HOLE_3: dummyfp3
UNK_HOLE_4: dummyfp4
UNK_HOLE_5: dummyfp5
UNK_HOLE_6: dummyfp6
UNK_HOLE_7: dummyfp7
UNK_HOLE_8: dummyfp8
UNK_HOLE_9: dummyfp9
UNK_HOLE_10: dummyfp10
UNK_HOLE_11: dummyfp11
UNK_HOLE_12: dummyfp12
UNK_HOLE_13: dummyfp13
UNK_HOLE_14: dummyfp14
UNK_HOLE_15: dummyfp15
UNK_HOLE_16: dummyfp16
UNK_HOLE_17: dummyfp17
UNK_HOLE_18: dummyfp18
UNK_HOLE_19: dummyfp19
UNK_HOLE_20: dummyfp20
UNK_HOLE_21: dummyfp21
UNK_HOLE_22: dummyfp22
UNK_HOLE_23: dummyfp23
UNK_HOLE_24: dummyfp24
UNK_HOLE_25: dummyfp25
UNK_HOLE_26: dummyfp26
UNK_HOLE_27: dummyfp27
UNK_HOLE_28: dummyfp28
UNK_HOLE_29: dummyfp29
UNK_HOLE_30: dummyfp30
UNK_HOLE_31: dummyfp31
UNK_HOLE_32: dummyfp32
UNK_HOLE_33: dummyfp33
UNK_HOLE_34: dummyfp34
UNK_HOLE_35: dummyfp35

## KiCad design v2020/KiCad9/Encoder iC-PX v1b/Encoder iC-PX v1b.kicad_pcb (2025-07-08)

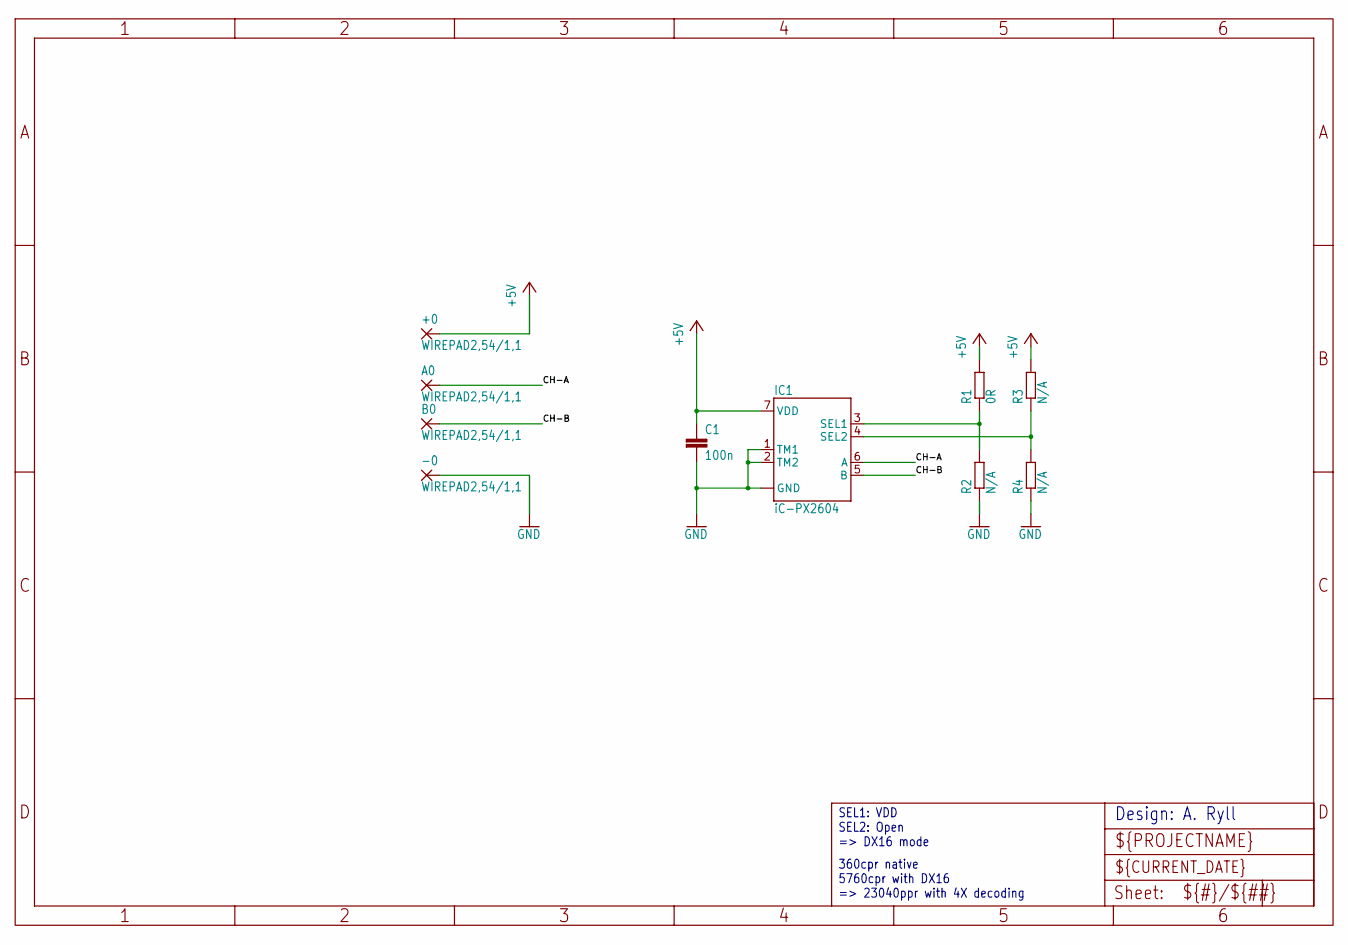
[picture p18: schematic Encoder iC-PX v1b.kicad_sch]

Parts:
+0: WIREPAD2,54/1,1; 2,54_1,1
-0: WIREPAD2,54/1,1; 2,54_1,1
A0: WIREPAD2,54/1,1; 2,54_1,1
B0: WIREPAD2,54/1,1; 2,54_1,1
C1: 100n; C0603
IC1: iC-PX2604; ODFN8-3X3
R1: 0R; R0603
R2, R3, R4: N/A; R0603

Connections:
+5V: +0.1, C1.1, IC1.7 (VDD), R1.2, R3.2
CH-A: A0.1, IC1.6 (A)
CH-B: B0.1, IC1.5 (B)
GND: -0.1, C1.2, IC1.1 (TM1), IC1.2 (TM2), IC1.8 (GND), IC1.BP (GND), R2.1, R4.1
SEL1: IC1.3 (SEL1), R1.1, R2.2
SEL2: IC1.4 (SEL2), R3.1, R4.2

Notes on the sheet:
360cpr native 5760cpr with DX16 => 23040ppr with 4X decoding
SEL1: VDD SEL2: Open => DX16 mode
Design: A. Ryll

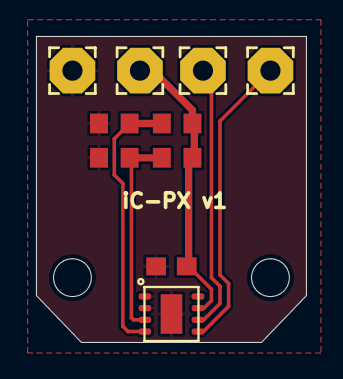
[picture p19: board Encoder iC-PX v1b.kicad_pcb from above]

Board: 2 copper layers, 15.0 x 17.0 mm, 12 parts (0 on the bottom side), 6 nets.

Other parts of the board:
UNK_HOLE_0: dummyfp0
UNK_HOLE_1: dummyfp1

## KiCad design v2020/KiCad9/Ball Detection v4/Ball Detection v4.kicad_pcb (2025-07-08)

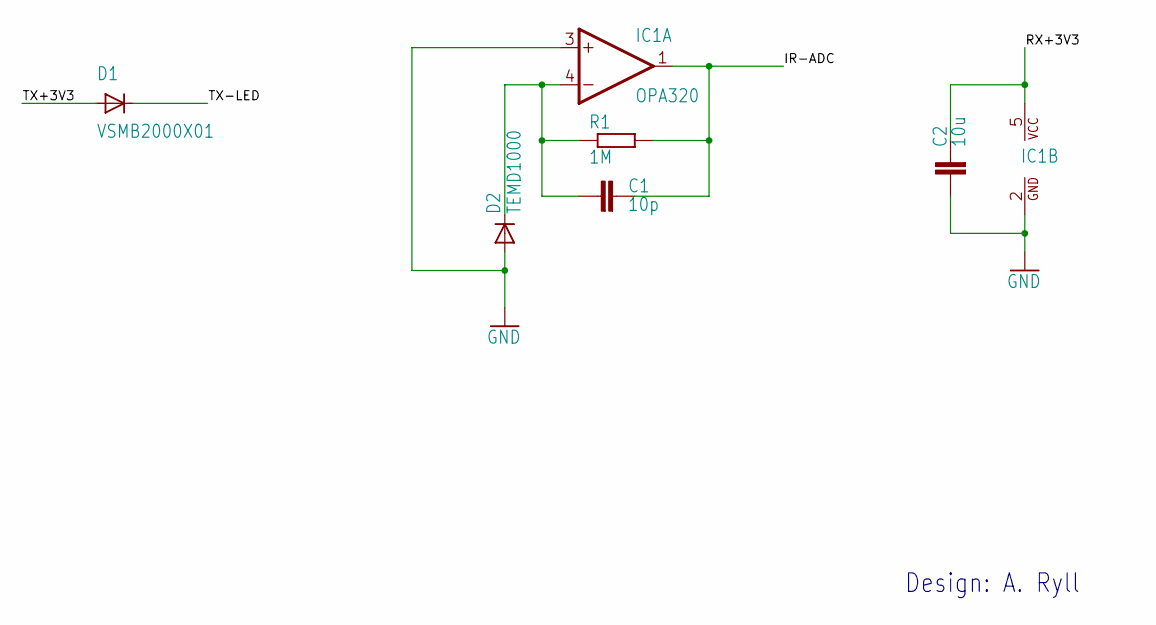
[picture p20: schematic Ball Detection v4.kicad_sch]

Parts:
C1: 10p; C0603
C2: 10u; C0603
D1: VSMB2000X01; LED-GULLR
D2: TEMD1000; LED-GULLR
IC1: OPA320; SOT23-5
R1: 1M; R0603

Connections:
GND: C2.1, D2.A, IC1.2 (GND), IC1.3 (+IN)
IR-ADC: C1.2, IC1.1 (OUT), R1.2
unnamed: C1.1, D2.C, IC1.4 (-IN), R1.1
NC: D1.C
RX+3V3: C2.2, IC1.5 (VCC)
TX-LED: D1.A

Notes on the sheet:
Design: A. Ryll

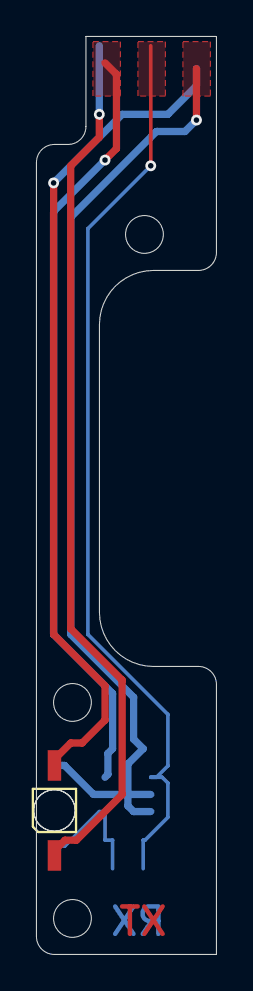
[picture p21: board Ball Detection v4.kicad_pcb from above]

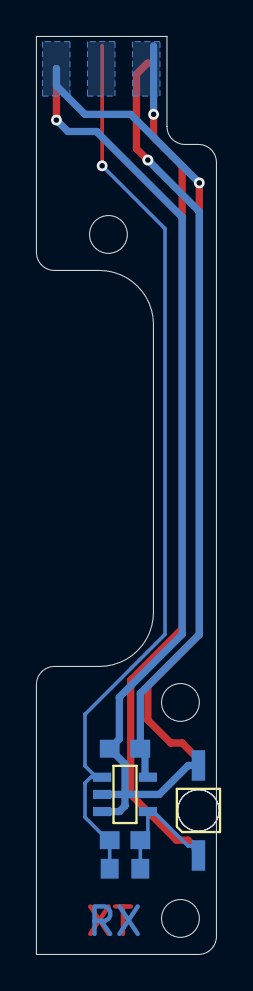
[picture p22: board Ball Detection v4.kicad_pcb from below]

Board: 2 copper layers, 10.0 x 51.0 mm, 9 parts (5 on the bottom side), 4 nets.

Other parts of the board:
UNK_HOLE_0: dummyfp0
UNK_HOLE_1: dummyfp1
UNK_HOLE_2: dummyfp2

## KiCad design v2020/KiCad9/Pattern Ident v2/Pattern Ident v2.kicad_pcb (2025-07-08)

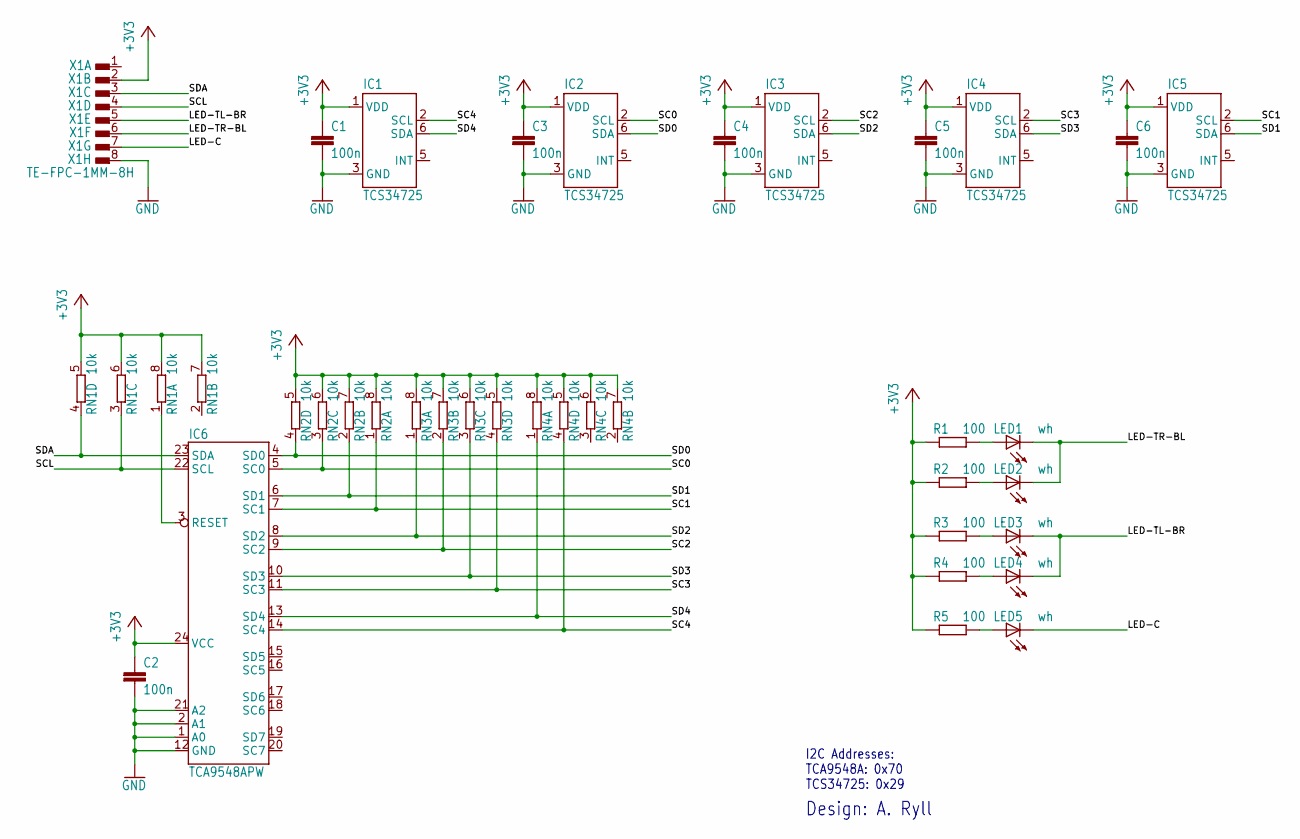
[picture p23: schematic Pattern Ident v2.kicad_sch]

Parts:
C1, C2, C3, C4, C5, C6: 100n; C0603
IC1, IC2, IC3, IC4, IC5: TCS34725; DFN6
IC6: TCA9548APW; TSSOP24
LED1, LED2, LED3, LED4, LED5: wh; CHIPLED_1206
R1, R2, R3, R4, R5: 100; R0603
RN1, RN2, RN3, RN4: 10k; EXB28V
X1: TE-FPC-1MM-8H; TE-84952-8

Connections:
+3V3: C1.1, C2.1, C3.1, C4.1, C5.1, C6.1, IC1.1 (VDD), IC2.1 (VDD), IC3.1 (VDD), IC4.1 (VDD), IC5.1 (VDD), IC6.24 (VCC), R1.1, R2.1, R3.1, R4.1, R5.1, RN1.5 (2), RN1.6 (2), RN1.7 (2), RN1.8 (2), RN2.5 (2), RN2.6 (2), RN2.7 (2), RN2.8 (2), RN3.5 (2), RN3.6 (2), RN3.7 (2), RN3.8 (2), RN4.5 (2), RN4.6 (2), RN4.7 (2), RN4.8 (2), X1.2
GND: C1.2, C2.2, C3.2, C4.2, C5.2, C6.2, IC1.3 (GND), IC2.3 (GND), IC3.3 (GND), IC4.3 (GND), IC5.3 (GND), IC6.1 (A0), IC6.2 (A1), IC6.12 (GND), IC6.21 (A2), X1.8
LED-C: LED5.C, X1.7
LED-TL-BR: LED3.C, LED4.C, X1.5
LED-TR-BL: LED1.C, LED2.C, X1.6
unnamed: LED1.A, R1.2
unnamed: LED2.A, R2.2
unnamed: LED3.A, R3.2
unnamed: LED4.A, R4.2
unnamed: LED5.A, R5.2
RESET: IC6.3 (RESET), RN1.1
SC0: IC2.2 (SCL), IC6.5 (SC0), RN2.3 (1)
SC1: IC5.2 (SCL), IC6.7 (SC1), RN2.1
SC2: IC3.2 (SCL), IC6.9 (SC2), RN3.2 (1)
SC3: IC4.2 (SCL), IC6.11 (SC3), RN3.4 (1)
SC4: IC1.2 (SCL), IC6.14 (SC4), RN4.4 (1)
SCL: IC6.22 (SCL), RN1.3 (1), X1.4
SD0: IC2.6 (SDA), IC6.4 (SD0), RN2.4 (1)
SD1: IC5.6 (SDA), IC6.6 (SD1), RN2.2 (1)
SD2: IC3.6 (SDA), IC6.8 (SD2), RN3.1
SD3: IC4.6 (SDA), IC6.10 (SD3), RN3.3 (1)
SD4: IC1.6 (SDA), IC6.13 (SD4), RN4.1
SDA: IC6.23 (SDA), RN1.4 (1), X1.3

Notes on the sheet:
I2C Addresses: TCA9548A: 0x70 TCS34725: 0x29
Design: A. Ryll

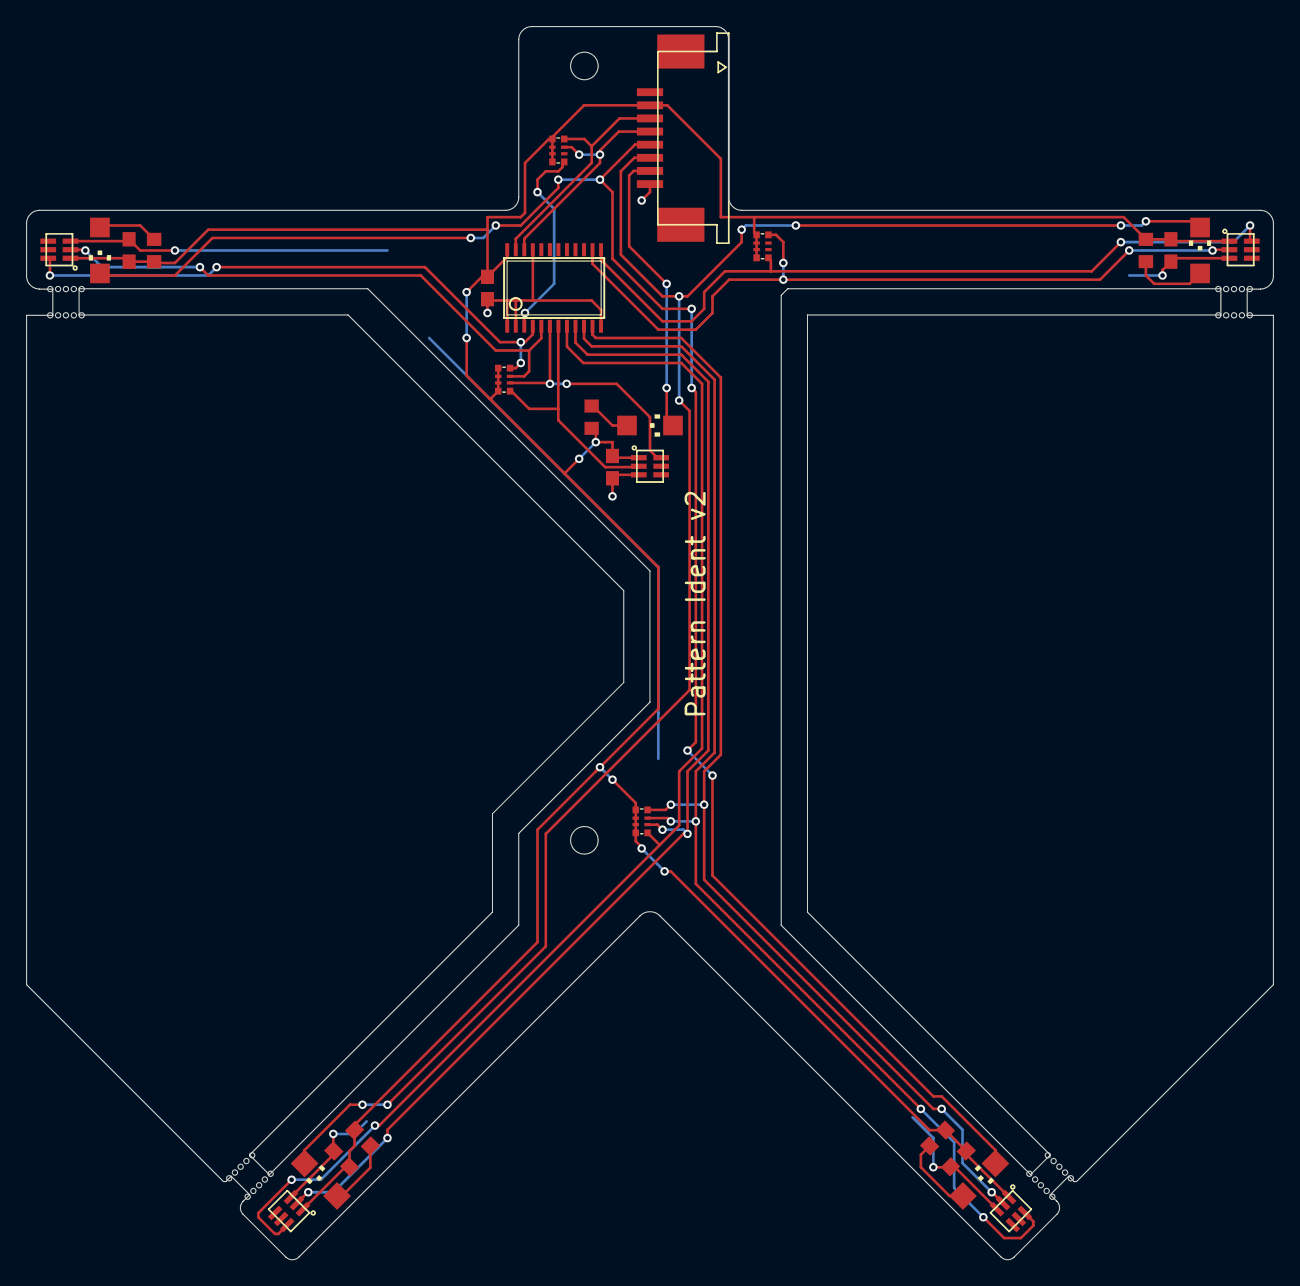
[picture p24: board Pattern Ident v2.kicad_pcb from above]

Board: 2 copper layers, 95.0 x 94.0 mm, 69 parts (0 on the bottom side), 23 nets.

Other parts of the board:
UNK_HOLE_0: dummyfp0
UNK_HOLE_1: dummyfp1
UNK_HOLE_2: dummyfp2
UNK_HOLE_3: dummyfp3
UNK_HOLE_4: dummyfp4
UNK_HOLE_5: dummyfp5
UNK_HOLE_6: dummyfp6
UNK_HOLE_7: dummyfp7
UNK_HOLE_8: dummyfp8
UNK_HOLE_9: dummyfp9
UNK_HOLE_10: dummyfp10
UNK_HOLE_11: dummyfp11
UNK_HOLE_12: dummyfp12
UNK_HOLE_13: dummyfp13
UNK_HOLE_14: dummyfp14
UNK_HOLE_15: dummyfp15
UNK_HOLE_16: dummyfp16
UNK_HOLE_17: dummyfp17
UNK_HOLE_18: dummyfp18
UNK_HOLE_19: dummyfp19
UNK_HOLE_20: dummyfp20
UNK_HOLE_21: dummyfp21
UNK_HOLE_22: dummyfp22
UNK_HOLE_23: dummyfp23
UNK_HOLE_24: dummyfp24
UNK_HOLE_25: dummyfp25
UNK_HOLE_26: dummyfp26
UNK_HOLE_27: dummyfp27
UNK_HOLE_28: dummyfp28
UNK_HOLE_29: dummyfp29
UNK_HOLE_30: dummyfp30
UNK_HOLE_31: dummyfp31
UNK_HOLE_32: dummyfp32
UNK_HOLE_33: dummyfp33
UNK_HOLE_34: dummyfp34
UNK_HOLE_35: dummyfp35
UNK_HOLE_36: dummyfp36
UNK_HOLE_37: dummyfp37
UNK_HOLE_38: dummyfp38
UNK_HOLE_39: dummyfp39
UNK_HOLE_40: dummyfp40
UNK_HOLE_41: dummyfp41

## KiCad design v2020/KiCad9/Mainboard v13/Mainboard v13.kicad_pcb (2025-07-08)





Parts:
ANT1: ANT-SMARA; ANT-SMA-RA; Digi-Key A97593-ND
C1, C2, C3, C6, C7, C8, C9, C10, C11, C12, C13, C14, C15, C16, C17, C18, C19, C21, C24, C26, C27, C29, C30, C31, C34, C36, C47, C49, C51, C57, C59: 100n; C0603; Digi-Key 1292-1397-1-ND
C4, C5, C20, C22, C23, C25, C28, C32, C54, C55: 10u; C0603; Digi-Key 478-5318-1-ND
C33: 0p5; C0402
C35, C37, C48, C50, C52: 1n; C0603; Digi-Key 399-1083-1-ND
C38: 100p; C0402
C39: 47p; C0402
C40: 0p8; C0402
C41: 1p5; C0402
C42, C44: NA; C0402; not fitted
C43: 0p6; C0402
C45: 1u; C0603; Digi-Key 1276-1860-1-ND
C46, C53: 10n; C0603; Digi-Key 399-1091-1-ND
C56, C58: 33u; C1206; Digi-Key 445-8046-1-ND
IC1: STM32H743ZST; LQFP144-ST; Digi-Key 497-17721-ND
IC2, IC6: STMPS2151STR; SOT23-5; Digi-Key 497-6856-1-ND
IC3: LT24; Digi-Key P0185-ND
IC4, IC5: MP34DT05; HCLGA4; Digi-Key 497-17809-1-ND
IC7: ICM-20689; QFN24-4X4-P; Digi-Key 1428-1059-1-ND
IC8: LIS3MDL; VFLGA-12; Digi-Key 497-13892-1-ND
IC9: SKY66112; SMCM-22; Digi-Key 863-1803-1-ND
IC10: SX1280; QFN24L; Digi-Key SX1280IMLTRTCT-ND
IC11: LP5907MFX-3.3; SOT23-5L; Digi-Key 296-38557-1-ND
IC12: LT3080ST; SOT223; Digi-Key LT3080EST#PBF-ND
IDD1: TE-FPC-1MM-8V; TE-1734248-8; Digi-Key WM6761CT-ND
L1, L2, L3, L4, L5, L6, L7: 120R; L0603; Digi-Key 490-1037-1-ND
L8: 470R; L1206; Digi-Key 490-16530-1-ND
LED1, LED3, LED4: gr; CHIP-LED0603; Digi-Key 732-4980-1-ND
LED2: rd; CHIP-LED0603; Digi-Key 732-4979-1-ND
LEDS1: TE-FPC-1MM-10H; TE-1-84952-0; Digi-Key A100250CT-ND
PAD1, PAD2, PAD3: WIREPAD5,4/3,0; 5,4_3,0; Digi-Key 732-7085-1-ND
PWR1: 4-1734742-0; TE-4-1734592-0; Digi-Key A100226CT-ND
Q1: ASE-4.000MHZ-LC-T; OSCI-ASE; Digi-Key 1253-1550-1-ND
Q2: FL520WFMT1; CRYSTAL-7M; Digi-Key FL520WFMT1CT-ND
R1, R2, R9, R10: 1k; R0603; Digi-Key 311-1.00KHRCT-ND
R3, R4: 10k; R0603; Digi-Key 311-10.0KHRCT-ND
R6: 3n; R0402
R7: 2n7; R0402
R8: 3n9; R0402
R11: 330k; R0603; Digi-Key YAG1637CT-ND
RN1, RN2, RN3, RN4, RN5, RN6, RN7, RN8, RN9, RN10, RN11, RN12: 100; EXB28V; Digi-Key Y7101CT-ND
SD1: SDCARD; Digi-Key A101492CT-ND
SW1: Reset; BUTTON4; Digi-Key 450-1130-ND
SW2: Power; KT11; Digi-Key CKN1859CT-ND
USB1: USBATE; USBA-TE; Digi-Key A118230CT-ND

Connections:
+3V3: C1.1, C3.1, C6.1, C7.1, C8.1, C9.1, C10.1, C11.1, C12.1, C13.1, C14.1, C15.1, C16.1, C17.1, C22.1, C23.1, C26.1, C30.1, C58.1, IC1.6 (VBAT), IC1.17 (VDD@1), IC1.30 (VDD@2), IC1.32 (VREF+), IC1.33 (VDDA), IC1.39 (VDD@3), IC1.52 (VDD@4), IC1.62 (VDD@5), IC1.72 (VDD@6), IC1.84 (VDD@7), IC1.95 (VUSB), IC1.108 (VDD@9), IC1.121 (VDD@10), IC1.131 (VDD@11), IC1.143 (PDR_ON), IC1.144 (VDD@12), IC4.1 (VDD), IC4.2 (LR), IC5.1 (VDD), IC7.8 (VDDIO), IC8.6 (VDDIO), IC12.2 (OUT), IC12.4 (OUT), L1.2, L2.2, L3.2, L4.2, Q1.1 (OE), Q1.4 (VCC), R1.2, R2.2, R10.2
+5V: C18.1, C24.1, IC3.11 (VCC5), IC6.5 (IN), L7.2, L8.1, LEDS1.1 (-1), PWR1.1 (-1), PWR1.2 (-1)
/BTN: PWR1.18 (-1), SW2.1
/CPS: IC9.15 (CPS), RN11.5 (2)
/CRX: IC9.2 (CRX), RN11.7 (2)
/CTX: IC9.17 (CTX), RN11.8 (2)
/DFSDM-CKOUT: IC1.28 (P2), IC4.3 (CLK), IC5.3 (CLK)
/DFSDM-DATIN0: IC1.27 (P1), IC4.4 (DOUT), IC5.4 (DOUT)
/FMC-A7: IC1.53 (P13), IC3.15 (RS)
/FMC-D0: IC1.85 (P14), IC3.9 (D0)
/FMC-D1: IC1.86 (P15), IC3.8 (D1)
/FMC-D2: IC1.114 (P0), IC3.7 (D2)
/FMC-D3: IC1.115 (P1), IC3.6 (D3)
/FMC-D4: IC1.58 (P7), IC3.16 (D4)
/FMC-D5: IC1.59 (P8), IC3.17 (D5)
/FMC-D6: IC1.60 (P9), IC3.18 (D6)
/FMC-D7: IC1.63 (P10), IC3.19 (D7)
/FMC-D8: IC1.64 (P11), IC3.20 (D8)
/FMC-D9: IC1.65 (P12), IC3.21 (D9)
/FMC-D10: IC1.66 (P13), IC3.22 (D10)
/FMC-D11: IC1.67 (P14), IC3.23 (D11)
/FMC-D12: IC1.68 (P15), IC3.24 (D12)
/FMC-D13: IC1.77 (P8), IC3.25 (D13)
/FMC-D14: IC1.78 (P9), IC3.26 (D14)
/FMC-D15: IC1.79 (P10), IC3.27 (D15)
/FMC-NE1: IC1.123 (P7), IC3.28 (CS)
/FMC-NOE: IC1.118 (P4), IC3.13 (RD)
/FMC-NWE: IC1.119 (P5), IC3.14 (WR)
/IDD0: IC1.87 (P2), IDD1.A2 (-1), IDD1.B2 (-1)
/IDD1: IC1.88 (P3), IDD1.A3 (-1), IDD1.B3 (-1)
/IDD2: IC1.89 (P4), IDD1.A4 (-1), IDD1.B4 (-1)
/IDD3: IC1.90 (P5), IDD1.A5 (-1), IDD1.B5 (-1)
/IDD4: IC1.91 (P6), IDD1.A6 (-1), IDD1.B6 (-1)
/IDD5: IC1.92 (P7), IDD1.A7 (-1), IDD1.B7 (-1)
/IDD6: IC1.93 (P8), IDD1.A8 (-1), IDD1.B8 (-1)
/IMU-CS: IC1.137 (P7), RN6.1
/IMU-INT: IC1.3 (P4), RN12.4 (1)
/JTAG-RESV1: IC1.110 (P15)
/JTAG-RESV2: IC1.133 (P3)
/JTAG-RESV3: IC1.134 (P4)
/KICK-CHG: IC1.126 (P11), PWR1.35 (-1)
/KICK-CS: IC1.127 (P12), PWR1.31 (-1)
/KICK-ERR: IC1.125 (P10), PWR1.38 (-1)
/KILL: IC1.122 (P6), PWR1.17 (-1)
/LCD-ON: IC1.55 (P15), RN4.5 (2)
/LCD-RESET: IC1.57 (P1), RN4.8 (2)
/LED1: IC1.26 (P0), LED1.C
/LED2: IC1.29 (P3), LED2.C
/MAG-CS: IC1.7 (P13), RN7.2 (1)
/MAG-DRDY: IC1.8 (P14), RN8.4 (1)
/MAG-INT: IC1.9 (P15), RN8.1
/OTG-FS-DM: IC1.103 (P11), RN5.4 (1)
/OTG-FS-DP: IC1.104 (P12), RN5.1
/PDN: IC1.117 (P3), PWR1.19 (-1)
/SD-CD: IC1.49 (P11), RN2.3 (1)
/SD-PWR: IC1.80 (P11), IC2.4 (EN), R3.1
/SD-WP: IC1.73 (P12), RN2.4 (1)
/SDMMC1-CK: IC1.113 (P12), RN3.4 (1)
/SDMMC1-CMD: IC1.116 (P2), RN3.3 (1)
/SDMMC1-D0: IC1.98 (P8), RN2.1
/SDMMC1-D1: IC1.99 (P9), RN2.2 (1)
/SDMMC1-D2: IC1.111 (P10), RN3.1
/SDMMC1-D3: IC1.112 (P11), RN3.2 (1)
/SMB-ALRT: IC1.12 (P2), PWR1.13 (-1)
/SMB-RST: IC1.128 (P13), PWR1.12 (-1)
/SMB-SCL: IC1.11 (P1), PWR1.15 (-1)
/SMB-SDA: IC1.10 (P0), PWR1.14 (-1)
/SPI1-MISO: IC1.42 (P6), RN9.2 (1)
/SPI1-MOSI: IC1.43 (P7), RN9.1
/SPI1-SCK: IC1.41 (P5), RN9.3 (1)
/SPI2-MISO: IC1.75 (P14), PWR1.33 (-1)
/SPI2-MOSI: IC1.76 (P15), PWR1.32 (-1)
/SPI2-SCK: IC1.74 (P13), PWR1.34 (-1)
/SPI4-MISO: IC1.4 (P5), RN1.8 (2), RN7.1, RN12.1
/SPI4-MOSI: IC1.5 (P6), RN1.6 (2), RN6.3 (1), RN7.3 (1)
/SPI4-SCK: IC1.1 (P2), RN1.5 (2), RN6.2 (1), RN7.4 (1)
/SRST: C2.1, IC1.25 (~RST), PWR1.28 (-1), SW1.1, SW1.2 (1)
/SWCLK: IC1.109 (P14), PWR1.26 (-1)
/SWDIO: IC1.105 (P13), PWR1.27 (-1)
/TIM1-CH1: IC1.100 (P8), PWR1.16 (-1)
/TIM3-CH1: IC1.96 (P6), LEDS1.2 (-1)
/TIM3-CH2: IC1.97 (P7), LEDS1.3 (-1)
/TIM3-CH3: IC1.46 (P0), LEDS1.4 (-1)
/TIM3-CH4: IC1.47 (P1), LEDS1.5 (-1)
/TIM4-CH1: IC1.81 (P12), LEDS1.6 (-1)
/TIM4-CH2: IC1.82 (P13), LEDS1.7 (-1)
/TIM4-CH3: IC1.139 (P8), LEDS1.8 (-1)
/TIM4-CH4: IC1.140 (P9), LEDS1.9 (-1)
/TIM13-CH1: IC1.20 (P8), PWR1.36 (-1)
/TIM14-CH1: IC1.21 (P9), PWR1.37 (-1)
/TP-CS: IC1.56 (P0), RN4.6 (2)
/TP-IRQ: IC1.40 (P4), RN1.7 (2)
/UART4-RX: IC1.35 (P1), PWR1.9 (-1)
/UART4-TX: IC1.34 (P0), PWR1.10 (-1)
/UART5-RX: IC1.135 (P5), PWR1.5 (-1)
/UART5-TX: IC1.136 (P6), PWR1.6 (-1)
/UART7-RX: IC1.18 (P6), PWR1.7 (-1)
/UART7-TX: IC1.19 (P7), PWR1.8 (-1)
/UART8-RX: IC1.141 (P0), PWR1.3 (-1)
/UART8-TX: IC1.142 (P1), PWR1.4 (-1)
/USART1-RX: IC1.102 (P10), PWR1.30 (-1)
/USART1-TX: IC1.101 (P9), PWR1.29 (-1)
/USART2-RX: IC1.37 (P3), PWR1.23 (-1)
/USART2-TX: IC1.36 (P2), PWR1.22 (-1)
/USART3-RX: IC1.70 (P11), PWR1.21 (-1)
/USART3-TX: IC1.69 (P10), PWR1.20 (-1)
/USART6-RX: IC1.124 (P9), PWR1.24 (-1)
/USART6-TX: IC1.129 (P14), PWR1.25 (-1)
/USB-ATT: IC1.132 (P15), PWR1.11 (-1)
/USB-EN: IC1.54 (P14), IC6.4 (EN), R4.2
/WF-3V3: C55.1, IC11.5 (VOUT), L5.1, L6.1, R9.2
/WF-BUSY: IC1.44 (P4), RN10.4 (1)
/WF-CPS: IC1.13 (P3), RN11.4 (1)
/WF-CRX: IC1.14 (P4), RN11.2 (1)
/WF-CS: IC1.22 (P10), RN9.4 (1)
/WF-CTX: IC1.15 (P5), RN11.1
/WF-IRQ: IC1.45 (P5), RN10.1
/WF-ON: IC1.48 (P2), IC11.3 (ON)
GND: ANT1.GND1 (GND), ANT1.GND2 (GND), ANT1.GND3 (GND), ANT1.GND4 (GND), C1.2, C2.2, C3.2, C4.2, C5.2, C6.2, C7.2, C8.2, C9.2, C10.2, C11.2, C12.2, C13.2, C14.2, C15.2, C16.2, C17.2, C18.2, C19.2, C20.2, C21.2, C22.2, C23.2, C24.2, C25.2, C26.2, C27.2, C28.2, C29.2, C30.2, C31.2, C32.2, C34.2, C35.2, C36.2, C37.2, C40.2, C41.2, C42.2, C43.2, C44.2, C45.2, C46.2, C47.2, C48.2, C49.2, C50.2, C51.2, C52.2, C53.2, C54.2, C55.2, C56.2, C57.2, C58.2, C59.2, IC1.16 (GND@1), IC1.31 (VSSA), IC1.38 (GND@2), IC1.51 (GND@3), IC1.61 (GND@4), IC1.83 (GND@5), IC1.94 (GND@6), IC1.107 (GND@7), IC1.120 (GND@8), IC1.130 (GND@9), IC1.138 (BOOT0), IC2.2 (GND), IC3.12 (GND@1), IC3.30 (GND@2), IC4.G1 (GND), IC4.G2 (GND), IC4.G3 (GND), IC4.G4 (GND), IC5.2 (LR), IC5.G1 (GND), IC5.G2 (GND), IC5.G3 (GND), IC5.G4 (GND), IC6.2 (GND), IC7.11 (FSYNC), IC7.18 (GND), IC8.2 (RSV1), IC8.3 (GND), IC8.12 (RSV2), IC9.1 (GND@1), IC9.4 (ANT_SEL), IC9.5 (GND@2), IC9.7 (GND@3), IC9.9 (GND@4), IC9.10 (GND@5), IC9.12 (GND@6), IC9.13 (GND@7), IC9.18 (GND@8), IC9.20 (GND@9), IC9.22 (GND@10), IC9.PAD1 (GND@11), IC9.PAD2 (GND@12), IC10.5 (GND@2), IC10.13 (GND@3), IC10.20 (GND@4), IC10.21 (GND@5), IC10.23 (GND@6), IC10.24 (GND@7), IC10.PAD (GND@1), IC11.2 (GND), LED3.C, LED4.C, LEDS1.10 (-1), PAD1.1, PAD2.1, PAD3.1, PWR1.39 (-1), PWR1.40 (-1), Q1.2 (GND), Q2.2 (GND1), Q2.4 (GND1), R3.2, R4.1, R11.1, RN6.4 (1), RN6.5 (2), RN8.2 (1), RN8.3 (1), RN10.2 (1), RN10.3 (1), RN10.6 (2), RN10.7 (2), RN12.2 (1), RN12.3 (1), RN12.6 (2), RN12.7 (2), SD1.3 (GND@1), SD1.6 (GND@2), SD1.COM1 (COM@1), SD1.COM2 (COM@2), SD1.COM3 (COM@3), SD1.COM4 (COM@4), SW1.3 (2), SW1.4 (2), SW2.2, USB1.4 (GND), USB1.MNT1 (S@1), USB1.MNT2 (S@2)
unnamed: ANT1.C (1), C44.1, R8.2
unnamed: C33.1, C41.1, R6.2, R7.1
unnamed: C33.2, C38.1, C42.1, R7.2
unnamed: C39.2, C43.1, R8.1
unnamed: C4.1, IC1.71 (VCAP@1)
unnamed: C5.1, IC1.106 (VCAP@2)
unnamed: IC1.23 (OSC_IN), Q1.3 (FO)
unnamed: C20.1, C21.1, IC2.5 (IN), L2.1
unnamed: IC2.1 (OUT), SD1.4 (VDD)
unnamed: IC3.40 (LCD_ON), RN4.4 (1)
unnamed: IC3.38 (RESET), RN4.1
unnamed: IC3.5 (TP_CLK), RN1.4 (1)
unnamed: IC3.39 (TP_CS), RN4.3 (1)
unnamed: IC3.4 (TP_DIN), RN1.3 (1)
unnamed: IC3.2 (TP_DOUT), RN1.1
unnamed: IC3.1 (TP_IRQ), RN1.2 (1)
unnamed: C19.1, IC3.29 (VCC3.3), L1.1
unnamed: IC6.1 (OUT), USB1.1 (+5V)
unnamed: IC7.9 (AD0/SDO), RN12.8 (2)
unnamed: IC7.12 (INT), RN12.5 (2)
unnamed: C25.1, IC7.10 (REGOUT)
unnamed: IC7.23 (SCL/SCLK), RN6.7 (2)
unnamed: IC7.24 (SDA/SDI), RN6.6 (2)
unnamed: C27.1, C28.1, IC7.13 (VDD), L3.1
unnamed: IC7.22 (~CS), RN6.8 (2)
unnamed: C29.1, IC8.4 (C1)
unnamed: IC8.8 (DRDY), RN8.5 (2)
unnamed: IC8.7 (INT), RN8.8 (2)
unnamed: IC8.9 (SA1/MISO), RN7.8 (2)
unnamed: IC8.1 (SCL/SCLK), RN7.5 (2)
unnamed: IC8.11 (SDA/MOSI), RN7.6 (2)
unnamed: C31.1, C32.1, IC8.5 (VDD), L4.1
unnamed: IC8.10 (~CS), RN7.7 (2)
unnamed: C39.1, IC9.8 (ANT1)
unnamed: C47.1, C48.1, C49.1, C50.1, C51.1, C52.1, IC9.3 (CSD), IC9.11 (VDD), IC9.14 (VCC2), IC9.16 (VCC1), IC9.19 (CHL), L6.2
unnamed: C38.2, IC9.21 (RFIN)
unnamed: IC10.7 (BUSY), RN10.5 (2)
unnamed: C45.1, C46.1, IC10.2 (VDD_IN), IC10.12 (DCC_FB)
unnamed: IC10.8 (DIO1), RN10.8 (2)
unnamed: IC10.16 (MISO), RN9.7 (2)
unnamed: IC10.17 (MOSI), RN9.8 (2)
unnamed: C40.1, IC10.22 (RFIO), R6.1
unnamed: IC10.18 (SCK), RN9.6 (2)
unnamed: C34.1, C35.1, C36.1, C37.1, IC10.3 (~RESET), IC10.11 (V_DIO), IC10.15 (VBAT), L5.2
unnamed: C53.1, IC10.1 (VR_PA)
unnamed: IC10.6 (XTA), Q2.1
unnamed: IC10.4 (XTB), Q2.3 (2)
unnamed: IC10.19 (~CS), RN9.5 (2)
unnamed: C54.1, IC11.1 (VIN), L7.1
unnamed: C56.1, C57.1, IC12.3 (IN), L8.2
unnamed: C59.1, IC12.1 (SET), R11.2
unnamed: LED1.A, R1.1
unnamed: LED2.A, R2.1
unnamed: LED3.A, R9.1
unnamed: LED4.A, R10.1
unnamed: RN2.8 (2), SD1.7 (D0)
unnamed: RN2.7 (2), SD1.8 (D1)
unnamed: RN2.6 (2), SD1.CD
unnamed: RN2.5 (2), SD1.WP
unnamed: RN3.8 (2), SD1.9 (D2)
unnamed: RN3.7 (2), SD1.1 (D3)
unnamed: RN3.6 (2), SD1.2 (CMD)
unnamed: RN3.5 (2), SD1.5 (CLK)
unnamed: RN5.8 (2), USB1.3 (D+)
unnamed: RN5.5 (2), USB1.2 (D-)

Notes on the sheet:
LDO 3.3V
Max output: 800mA (110°C)
DIS2
Wireless Interface
USB Host
Kicker
IMU
Buzzer
SD Card
Connectors
DIS1
Main Processor
LCD
2mA
Magnetometer
Microphones



Board: 4 copper layers, 80.0 x 85.0 mm, 118 parts (3 on the bottom side), 181 nets.

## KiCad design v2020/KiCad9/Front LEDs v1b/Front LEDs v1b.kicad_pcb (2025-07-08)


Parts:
IC1, IC2, IC3, IC4, IC5, IC6, IC7, IC8: BCR421UE; SOT26
LED1, LED2: 1W RGBW; CREE-XLAMP; PARTNR XMLCTW-A0-0000-00C2AAAB1
R1, R2, R3, R4, R5, R6, R7, R8: 4R7; R0805
X1: TE-FPC-1MM-10H; TE-1-84952-0

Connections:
+5V: LED1.1 (A), LED1.2 (A), LED1.3 (A), LED1.4 (A), LED2.1 (A), LED2.2 (A), LED2.3 (A), LED2.4 (A), X1.10
GND: IC1.4 (GND), IC2.4 (GND), IC3.4 (GND), IC4.4 (GND), IC5.4 (GND), IC6.4 (GND), IC7.4 (GND), IC8.4 (GND), R1.1, R2.1, R3.1, R4.1, R5.1, R6.1, R7.1, R8.1, X1.1
unnamed: IC1.2 (OUT), IC1.3 (OUT), IC1.5 (OUT), LED1.8 (C)
unnamed: IC1.6 (REXT), R1.2
unnamed: IC3.2 (OUT), IC3.3 (OUT), IC3.5 (OUT), LED1.7 (C)
unnamed: IC3.6 (REXT), R3.2
unnamed: IC5.2 (OUT), IC5.3 (OUT), IC5.5 (OUT), LED1.6 (C)
unnamed: IC5.6 (REXT), R5.2
unnamed: IC7.2 (OUT), IC7.3 (OUT), IC7.5 (OUT), LED1.5 (C)
unnamed: IC7.6 (REXT), R7.2
unnamed: IC2.2 (OUT), IC2.3 (OUT), IC2.5 (OUT), LED2.8 (C)
unnamed: IC2.6 (REXT), R2.2
unnamed: IC4.2 (OUT), IC4.3 (OUT), IC4.5 (OUT), LED2.7 (C)
unnamed: IC4.6 (REXT), R4.2
unnamed: IC6.2 (OUT), IC6.3 (OUT), IC6.5 (OUT), LED2.6 (C)
unnamed: IC6.6 (REXT), R6.2
unnamed: IC8.2 (OUT), IC8.3 (OUT), IC8.5 (OUT), LED2.5 (C)
unnamed: IC8.6 (REXT), R8.2
TIM3-CH1: IC1.1 (EN), X1.2
TIM3-CH2: IC3.1 (EN), X1.3
TIM3-CH3: IC5.1 (EN), X1.4
TIM3-CH4: IC7.1 (EN), X1.5
TIM4-CH1: IC2.1 (EN), X1.6
TIM4-CH2: IC4.1 (EN), X1.7
TIM4-CH3: IC6.1 (EN), X1.8
TIM4-CH4: IC8.1 (EN), X1.9

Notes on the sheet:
LED: Cree XMLCTW-A0-0000-00C2AAAB1
Design: A. Ryll


Board: 2 copper layers, 82.0 x 14.0 mm, 25 parts (0 on the bottom side), 26 nets.

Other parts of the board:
UNK_HOLE_0: dummyfp0
UNK_HOLE_1: dummyfp1
UNK_HOLE_2: dummyfp2
UNK_HOLE_3: dummyfp3
UNK_HOLE_4: dummyfp4
UNK_HOLE_5: dummyfp5

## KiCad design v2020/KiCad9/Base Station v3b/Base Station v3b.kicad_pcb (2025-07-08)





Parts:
C1, C2, C3, C4, C5, C6, C7, C8, C11, C14, C16, C19, C20, C21, C22, C23, C24, C25, C26, C27, C28, C29, C30, C31, C34, C36, C50, C52, C54: 100n; C0603
C9, C10, C15, C17, C18, C32, C57, C58: 10u; C0603
C12, C13: 3p; C0603
C33, C44: 0p5; C0402
C35, C37, C51, C53, C55, C59, C60, C61, C62: 1n; C0603
C38: 100p; C0402
C39, C47: 47p; C0402
C40, C43, C48: NA; C0402
C41, C42: 1p2; C0402
C45: 1u; C0603
C46, C56: 10n; C0603
C49: 0p7; C0402
ETH1: SI-60062-F; RJ45-LED
IC1: 741G125DBV; SOT23-5
IC2: FT2232ST; LQFP48-ST
IC3: SC189-3.3; SOT23-5
IC4: 9376?B; SOT23-6
IC5: STM32F767VIT6; LQFP100-ST
IC6: CP11009; CP11009-THX
IC7: DP83848CVV; LQFP48
IC8: SKY66112; SMCM-22
IC9: SX1280; QFN24L
IC10: LP5907MFX-3.3; SOT23-5L
L1, L3, L4, L5: 120R; 0603
L2: 2u2; IHLP1616
LED1: rd; CHIP-LED0603
LED2, LED3: gr; CHIP-LED0603
PWR1: gr; CHIP-LED0603
Q1: CSTCR6M00G55-R0; CSTCR6M
Q2: ABS07W-32.768KHZ; CRYSTAL-07W
Q3: 25MHz; 7X
Q4: FL520WFMT1; CRYSTAL-7M
R1, R6, R7, R9, R10, R11, R12, R13, R22: 1k; R0603
R2, R3: 33; R0603
R4, R14: 1k5; R0603
R5: 1M; R0603
R8, R17: 4k87; R0603
R15, R16: 2k2; R0603
R18, R21: 3n; R0402
R19, R20: 2n4; R0402
RESET1: BUTTON4
RN1: 10k; EXB28V
RN2, RN3, RN4, RN5, RN6, RN8, RN9, RN10, RN11, RN12: 100; EXB28V
RN7: N/A; EXB28V
UNK100MBIT1: gr; CHIP-LED0603
USB1: USB-BU; USB-BMICRO
X1: 3034TR; CR2025
X2, X3: ANT-SMA-EDGERA; ANT-SMA-RA

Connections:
25MHZ: IC5.12 (OSC_IN), IC7.25 (25MHZ_OUT)
+3V3: C3.1, C4.1, C5.1, C10.1, C16.1, C19.1, C20.1, C21.1, C22.1, C23.1, C24.1, C25.1, C26.1, C27.1, C28.1, ETH1.2 (TCT), ETH1.5 (RCT), IC1.5 (VCC), IC2.10 (SI/WUA), IC2.14 (VCCIOA), IC2.26 (SI/WUB), IC2.31 (VCCIOB), IC3.4 (FB), IC5.11 (VDD@1), IC5.20 (VREF+), IC5.21 (VDDA), IC5.27 (VDD@2), IC5.50 (VDD@3), IC5.75 (VDD@4), IC5.100 (VDD@5), IC7.22 (AVDD33), IC7.32 (IOVDD33@1), IC7.48 (IOVDD33@2), L2.P$1 (1), L3.2, Q3.1 (OE), Q3.4 (VCC), R6.2, R9.2, R10.2, R11.2, R12.2, R13.2, R14.2, R15.2, R16.2, RN1.5 (2), RN1.7 (2), RN1.8 (2), RN5.5 (2), RN5.6 (2), RN5.7 (2), RN5.8 (2), RN7.5 (2), RN7.6 (2), RN7.7 (2), RN7.8 (2); also elsewhere on the board
+5V: C6.1, C7.1, C9.1, C11.1, C58.1, IC2.3 (VCC1), IC2.4 (RESET), IC2.42 (VCC2), IC3.1 (VIN), IC3.3 (EN), IC4.6 (VCC), IC10.1 (VIN), L1.2, R1.2, R8.2
ANTS: C59.1, IC8.4 (ANT_SEL), RN12.8 (2)
CPS: C62.1, IC8.15 (CPS), RN12.6 (2)
CRX: C61.1, IC8.2 (CRX), RN12.7 (2)
CTX: C60.1, IC8.17 (CTX), RN12.5 (2)
FMC_A16: IC5.58 (P11), IC6.4 (RS)
FMC_D0: IC5.61 (P14), IC6.21 (D0)
FMC_D1: IC5.62 (P15), IC6.22 (D1)
FMC_D2: IC5.81 (P0), IC6.23 (D2)
FMC_D3: IC5.82 (P1), IC6.24 (D3)
FMC_D4: IC5.37 (P7), IC6.25 (D4)
FMC_D5: IC5.38 (P8), IC6.26 (D5)
FMC_D6: IC5.39 (P9), IC6.27 (D6)
FMC_D7: IC5.40 (P10), IC6.28 (D7)
FMC_D8: IC5.41 (P11), IC6.7 (D8)
FMC_D9: IC5.42 (P12), IC6.8 (D9)
FMC_D10: IC5.43 (P13), IC6.9 (D10)
FMC_D11: IC5.44 (P14), IC6.10 (D11)
FMC_D12: IC5.45 (P15), IC6.11 (D12)
FMC_D13: IC5.55 (P8), IC6.12 (D13)
FMC_D14: IC5.56 (P9), IC6.13 (D14)
FMC_D15: IC5.57 (P10), IC6.14 (D15)
FMC_NE1: IC5.88 (P7), IC6.15 (CS)
FMC_NOE: IC5.85 (P4), IC6.6 (RD)
FMC_NWE: IC5.86 (P5), IC6.5 (WR)
GND: C1.2, C2.2, C3.2, C4.2, C5.2, C6.2, C7.2, C8.2, C9.2, C10.2, C11.2, C12.2, C13.2, C14.2, C15.2, C16.2, C17.2, C18.2, C19.2, C20.2, C21.2, C22.2, C23.2, C24.2, C25.2, C26.2, C27.2, C28.2, C29.2, C30.2, C31.2, C32.2, C34.2, C35.2, C36.2, C37.2, C40.2, C41.2, C42.2, C43.2, C44.2, C45.2, C46.2, C48.2, C49.2, C50.2, C51.2, C52.2, C53.2, C54.2, C55.2, C56.2, C57.2, C58.2, C59.2, C60.2, C61.2, C62.2, ETH1.8 (CHSGND), ETH1.9 (SHIELD@1), ETH1.10 (SHIELD@2), IC1.3 (GND), IC2.9 (GND1), IC2.18 (GND2), IC2.25 (GND3), IC2.34 (GND4), IC2.45 (AGND), IC2.47 (TEST), IC3.2 (GND), IC4.2 (GND), IC5.10 (GND@1), IC5.19 (VSSA), IC5.26 (GND@2), IC5.49 (GND@3), IC5.74 (GND@4), IC5.94 (BOOT0), IC5.99 (GND@5), IC6.1 (GND), IC7.15 (AGND@1), IC7.19 (AGND@2), IC7.35 (IOGND@1), IC7.36 (DGND), IC7.47 (IOGND@2), IC8.1 (GND@1), IC8.5 (GND@2), IC8.7 (GND@3), IC8.9 (GND@4), IC8.10 (GND@5), IC8.12 (GND@6), IC8.13 (GND@7), IC8.18 (GND@8), IC8.20 (GND@9), IC8.22 (GND@10), IC8.PAD1 (GND@11), IC8.PAD2 (GND@12), IC9.5 (GND@2), IC9.13 (GND@3), IC9.20 (GND@4), IC9.21 (GND@5), IC9.23 (GND@6), IC9.24 (GND@7), IC9.PAD (GND@1), IC10.2 (GND), LED3.C, PWR1.C, Q1.2, Q3.2 (GND), Q4.2 (GND1), Q4.4 (GND2), R17.1, RESET1.1, RESET1.2, RN1.6 (2), USB1.5 (GND), X1.GND, X2.GND1 (GND), X2.GND2 (GND1), X2.GND3 (GND2), X2.GND4 (GND3), X3.GND1 (GND), X3.GND2 (GND1), X3.GND3 (GND2), X3.GND4 (GND3); also elsewhere on the board
JTAG_UNUSED1: IC5.77 (P15)
JTAG_UNUSED2: IC5.89 (P3)
JTD-A2M1: IC1.2 (I), IC2.23 (ADBUS1), RN1.2 (1)
JTD-M2A1: IC2.22 (ADBUS2), RN2.4 (1)
LCD_ON: IC5.69 (P10), IC6.19 (LCD_ON)
LCD_RESET: IC5.68 (P9), IC6.17 (RESET)
LED0: IC5.28 (P4), LED2.C
LED1: IC5.29 (P5), LED1.C
MII_COL: IC5.25 (P3), RN8.2 (1)
MII_CRS: IC5.22 (P0), RN9.4 (1)
MII_INT: IC5.4 (P5), IC7.7 (PWR_DOWN/INT)
MII_MDC: IC5.16 (P1), IC7.31 (MDC)
MII_MDIO: IC5.24 (P2), IC7.30 (MDIO), R14.1
MII_RXD0: IC5.32 (P4), RN8.3 (1)
MII_RXD1: IC5.33 (P5), RN8.4 (1)
MII_RXD2: IC5.34 (P0), RN6.1
MII_RXD3: IC5.35 (P1), RN6.2 (1)
MII_RX_CLK: IC5.23 (P1), RN9.2 (1)
MII_RX_DV: IC5.31 (P7), RN9.3 (1)
MII_RX_ER: IC5.46 (P10), RN8.1
MII_TXD0: IC5.51 (P12), RN4.1
MII_TXD1: IC5.52 (P13), RN4.2 (1)
MII_TXD2: IC5.17 (P2), RN4.3 (1)
MII_TXD3: IC5.95 (P8), RN4.4 (1)
MII_TX_CLK: IC5.18 (P3), RN6.3 (1)
MII_TX_EN: IC5.47 (P11), RN6.4 (1)
unnamed: IC9.17 (MOSI), RN10.6 (2)
unnamed: IC9.16 (MISO), RN10.5 (2)
unnamed: IC9.18 (SCK), RN10.7 (2)
unnamed: IC9.19 (~CS), RN10.8 (2)
unnamed: IC9.7 (BUSY), RN11.8 (2)
unnamed: C18.1, IC5.73 (VCAP@2)
unnamed: IC9.8 (DIO1), RN11.5 (2)
unnamed: IC2.48 (EECS), IC4.5 (CS)
unnamed: IC2.1 (EESK), IC4.4 (CLK)
unnamed: IC7.3 (TXD_0), RN4.8 (2)
unnamed: IC7.4 (TXD_1), RN4.7 (2)
unnamed: IC7.5 (TXD_2), RN4.6 (2)
unnamed: IC2.2 (EEDATA), IC4.3 (DI), R7.2
unnamed: IC7.6 (TXD_3), RN4.5 (2)
unnamed: IC7.1 (TX_CLK), RN6.6 (2)
unnamed: IC7.2 (TX_EN), RN6.5 (2)
unnamed: IC7.45 (RXD_2), RN6.8 (2)
unnamed: LED3.A, R22.1
unnamed: IC2.44 (XTOUT), Q1.3, R5.1
unnamed: IC4.1 (DO), R7.1, R8.1
unnamed: IC7.46 (RXD_3), RN6.7 (2)
unnamed: C17.1, IC5.48 (VCAP@1)
unnamed: IC7.43 (RXD_0), RN8.6 (2)
unnamed: IC7.44 (RXD_1), RN8.5 (2)
unnamed: IC7.42 (COL), RN8.7 (2)
unnamed: IC7.41 (RX_ER), RN8.8 (2)
unnamed: IC7.39 (RX_DV), RN9.6 (2)
unnamed: IC7.38 (RX_CLK), RN9.7 (2)
unnamed: IC7.40 (CRS/CRS_DV), RN9.5 (2)
unnamed: IC7.24 (RBIAS), R17.2
unnamed: C29.1, C30.1, C31.1, C32.1, IC7.18 (PFBIN1), IC7.23 (PFBOUT), IC7.37 (PFBIN2)
unnamed: IC7.20 (RESV@1), R15.1
unnamed: IC7.21 (RESV@2), R16.1
unnamed 87: ETH1.12 (LED_YE-), IC7.26 (LED_ACT/COL), RN7.3 (1); also elsewhere on the board
unnamed 88: IC7.27 (LED_SPEED), RN7.2 (1), UNK100MBIT1.C; also elsewhere on the board
unnamed 89: ETH1.14 (LED_GR-), IC7.28 (LED_LINK), RN7.1; also elsewhere on the board
unnamed 90: ETH1.6 (RD-), IC7.13 (RD-), RN5.4 (1); also elsewhere on the board
unnamed 91: PWR1.A, R6.1; also elsewhere on the board
unnamed 92: ETH1.4 (RD+), IC7.14 (RD+), RN5.3 (1); also elsewhere on the board
unnamed 93: ETH1.3 (TD-), IC7.16 (TD-), RN5.2 (1); also elsewhere on the board
unnamed 94: ETH1.1 (TD+), IC7.17 (TD+), RN5.1; also elsewhere on the board
unnamed 95: R11.1, UNK100MBIT1.A; also elsewhere on the board
unnamed 96: ETH1.13 (LED_GR+), R12.1; also elsewhere on the board
unnamed 97: ETH1.11 (LED_YE+), R13.1; also elsewhere on the board
unnamed: IC7.34 (X1), Q3.3 (FO)
unnamed: IC1.4 (O), RN2.1
unnamed: LED2.A, R10.1
unnamed: LED1.A, R9.1
unnamed: IC2.40 (BDBUS0), RN3.4 (1)
unnamed: IC2.39 (BDBUS1), RN3.1
unnamed: C15.1, IC6.2 (VCC3.3), L3.1
unnamed: IC9.6 (XTA), Q4.1
unnamed: IC9.4 (XTB), Q4.3 (2)
unnamed: C33.1, C41.1, R18.2, R19.1
unnamed: C33.2, C38.2, C42.1, R19.2
unnamed: C56.1, IC9.1 (VR_PA)
unnamed: C45.1, C46.1, IC9.2 (VDD_IN), IC9.12 (DCC_FB)
unnamed: C38.1, IC8.21 (RFIN)
unnamed: C39.2, C43.1, R20.1
unnamed: C44.1, R20.2, X2.C (1)
unnamed: C47.2, C48.1, R21.1
unnamed: C49.1, R21.2, X3.C (1)
unnamed: C39.1, IC8.8 (ANT1)
unnamed: C47.1, IC8.6 (ANT2)
unnamed: IC2.7 (USBDP), R3.2, R4.2
unnamed: IC2.8 (USBDM), R2.2
unnamed: IC2.5 (RSTOUT), R4.1
unnamed: C2.1, IC2.6 (3V3OUT)
unnamed: C8.1, L1.1, USB1.1 (VCC)
unnamed: R2.1, USB1.2 (D-)
unnamed: R3.1, USB1.3 (D+)
unnamed: C1.1, IC2.46 (AVCC), R1.1
unnamed: IC2.43 (XTIN), Q1.1, R5.2
OSC32_IN: C12.1, IC5.8 (P14), Q2.1
OSC32_OUT: C13.1, IC5.9 (P15), Q2.2
PHY_RESET: IC5.30 (P6), IC7.29 (RESET_N)
RFIO1: C40.1, IC9.22 (RFIO), R18.1
SPI2_MISO: IC5.53 (P14), IC6.33 (TP_DOUT)
SPI2_MOSI: IC5.54 (P15), IC6.31 (TP_DIN)
SPI2_SCK: IC5.71 (P12), IC6.29 (TP_CLK)
SPI3_MISO: IC5.79 (P11), RN10.4 (1)
SPI3_MOSI: IC5.80 (P12), RN10.3 (1)
SPI3_SCK: IC5.78 (P10), RN10.2 (1)
SRST: C14.1, IC2.15 (ACBUS0), IC5.14 (~RST), RESET1.3, RESET1.4, RN1.4 (1)
SW-OUT: IC3.5 (SW), L2.P$2 (2)
SWCLK: IC5.76 (P14), RN2.6 (2)
SWCLK1: IC2.24 (ADBUS0), RN1.3 (1), RN2.3 (1)
SWDIO: IC5.72 (P13), RN2.5 (2), RN2.8 (2)
SWDIO_OE: IC1.1 (OE), IC2.21 (ADBUS3), RN1.1
TP_CS: IC5.63 (P6), IC6.30 (TP_CS)
TP_IRQ: IC5.59 (P12), IC6.34 (TP_IRQ)
USART1_RX: IC5.93 (P7), RN3.5 (2)
USART1_TX: IC5.92 (P6), RN3.8 (2)
VBAT: IC5.6 (VBAT), X1.POS1, X1.POS2
WF1_BUSY: IC5.83 (P2), RN11.1
WF1_CS: IC5.87 (P6), RN10.1
WF1_IRQ: IC5.84 (P3), RN11.4 (1)
WF_3V3: C57.1, IC10.5 (VOUT), L4.1, L5.1, R22.2
WF_3V3FEM: C50.1, C51.1, C52.1, C53.1, C54.1, C55.1, IC8.3 (CSD), IC8.11 (VDD), IC8.14 (VCC2), IC8.16 (VCC1), IC8.19 (CHL), L5.2
WF_3V3SX: C34.1, C35.1, C36.1, C37.1, IC9.3 (~RESET), IC9.11 (V_DIO), IC9.15 (VBAT), L4.2
WF_ANT: IC5.5 (P6), RN12.1
WF_CPS: IC5.1 (P2), RN12.3 (1)
WF_CRX: IC5.3 (P4), RN12.2 (1)
WF_CTX: IC5.2 (P3), RN12.4 (1)
WF_ON: IC5.91 (P5), IC10.3 (ON)

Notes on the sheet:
LCD
SX1280: 35mA
Do not use PB4~~{}
USB
52°C @ 160mA
Ethernet PHY
Wireless Interface
Main Processor
SWD+UART
92mA
130mA
SKY: 125mA
Power
RF FEM: SKY66112-11


Board: 4 copper layers, 58.0 x 85.0 mm, 130 parts (0 on the bottom side), 157 nets.

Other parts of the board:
ETH0: SI-60062-F; RJ45-LED
PWR0: gr; CHIP-LED0603
U$1: BMI-S-204-F; SHIELD-32MM
UNK100MBIT0: gr; CHIP-LED0603
UNK_HOLE_0: dummyfp0
UNK_HOLE_1: dummyfp1
UNK_HOLE_2: dummyfp2

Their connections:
+3V3: ETH0.2, ETH0.5; also elsewhere on the board
GND: ETH0.8, ETH0.9, ETH0.10, PWR0.C; also elsewhere on the board
unnamed 87: ETH0.12; also elsewhere on the board
unnamed 88: UNK100MBIT0.C; also elsewhere on the board
unnamed 89: ETH0.14; also elsewhere on the board
unnamed 90: ETH0.6; also elsewhere on the board
unnamed 91: PWR0.A; also elsewhere on the board
unnamed 92: ETH0.4; also elsewhere on the board
unnamed 93: ETH0.3; also elsewhere on the board
unnamed 94: ETH0.1; also elsewhere on the board
unnamed 95: UNK100MBIT0.A; also elsewhere on the board
unnamed 96: ETH0.13; also elsewhere on the board
unnamed 97: ETH0.11; also elsewhere on the board

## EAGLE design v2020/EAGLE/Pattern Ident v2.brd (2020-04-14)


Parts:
C1, C2, C3, C4, C5, C6: 100n; C0603
IC1, IC2, IC3, IC4, IC5: TCS34725; DFN6
IC6: TCA9548APW; TSSOP24
LED1, LED2, LED3, LED4, LED5: wh; CHIPLED_1206
R1, R2, R3, R4, R5: 100; R0603
RN1, RN2, RN3, RN4: 10k; EXB28V
X1: TE-FPC-1MM-8H; TE-84952-8

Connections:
+3V3: C1.1, C2.1, C3.1, C4.1, C5.1, C6.1, IC1.1 (VDD), IC2.1 (VDD), IC3.1 (VDD), IC4.1 (VDD), IC5.1 (VDD), IC6.24 (VCC), R1.1, R2.1, R3.1, R4.1, R5.1, RN1.5 (2), RN1.6 (2), RN1.7 (2), RN1.8 (2), RN2.5 (2), RN2.6 (2), RN2.7 (2), RN2.8 (2), RN3.5 (2), RN3.6 (2), RN3.7 (2), RN3.8 (2), RN4.5 (2), RN4.6 (2), RN4.7 (2), RN4.8 (2), X1.2
GND: C1.2, C2.2, C3.2, C4.2, C5.2, C6.2, IC1.3 (GND), IC2.3 (GND), IC3.3 (GND), IC4.3 (GND), IC5.3 (GND), IC6.1 (A0), IC6.2 (A1), IC6.12 (GND), IC6.21 (A2), X1.8
LED-C: LED5.C, X1.7
LED-TL-BR: LED3.C, LED4.C, X1.5
LED-TR-BL: LED1.C, LED2.C, X1.6
unnamed: LED1.A, R1.2
unnamed: LED2.A, R2.2
unnamed: LED3.A, R3.2
unnamed: LED4.A, R4.2
unnamed: LED5.A, R5.2
RESET: IC6.3 (RESET), RN1.1
SC0: IC2.2 (SCL), IC6.5 (SC0), RN2.3 (1)
SC1: IC5.2 (SCL), IC6.7 (SC1), RN2.1
SC2: IC3.2 (SCL), IC6.9 (SC2), RN3.2 (1)
SC3: IC4.2 (SCL), IC6.11 (SC3), RN3.4 (1)
SC4: IC1.2 (SCL), IC6.14 (SC4), RN4.4 (1)
SCL: IC6.22 (SCL), RN1.3 (1), X1.4
SD0: IC2.6 (SDA), IC6.4 (SD0), RN2.4 (1)
SD1: IC5.6 (SDA), IC6.6 (SD1), RN2.2 (1)
SD2: IC3.6 (SDA), IC6.8 (SD2), RN3.1
SD3: IC4.6 (SDA), IC6.10 (SD3), RN3.3 (1)
SD4: IC1.6 (SDA), IC6.13 (SD4), RN4.1
SDA: IC6.23 (SDA), RN1.4 (1), X1.3

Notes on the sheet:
I2C Addresses: TCA9548A: 0x70 TCS34725: 0x29
Design: A. Ryll


Board: 2 copper layers, 95.0 x 94.0 mm, 27 parts (0 on the bottom side), 23 nets.

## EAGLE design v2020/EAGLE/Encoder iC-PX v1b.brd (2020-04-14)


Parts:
+: WIREPAD2,54/1,1; 2,54/1,1
-: WIREPAD2,54/1,1; 2,54/1,1
A: WIREPAD2,54/1,1; 2,54/1,1
B: WIREPAD2,54/1,1; 2,54/1,1
C1: 100n; C0603
IC1: iC-PX2604; ODFN8-3X3
R1: 0R; R0603
R2, R3, R4: N/A; R0603

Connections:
+5V: +.1, C1.1, IC1.7 (VDD), R1.2, R3.2
CH-A: A.1, IC1.6 (A)
CH-B: B.1, IC1.5 (B)
GND: -.1, C1.2, IC1.1 (TM1), IC1.2 (TM2), IC1.8 (GND), IC1.BP (GND), R2.1, R4.1
SEL1: IC1.3 (SEL1), R1.1, R2.2
SEL2: IC1.4 (SEL2), R3.1, R4.2

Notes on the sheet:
SEL1: VDD SEL2: Open => DX16 mode
360cpr native 5760cpr with DX16 => 23040ppr with 4X decoding
Design: A. Ryll


Board: 2 copper layers, 15.0 x 17.0 mm, 10 parts (0 on the bottom side), 6 nets.

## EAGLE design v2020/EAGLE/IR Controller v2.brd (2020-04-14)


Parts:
C1, C2, C4, C5, C7, C9, C11, C13, C15: 100n; C0603
C3: 1u; C0603
C6, C8, C10, C12, C14: 1p; C0603
D1, D3, D5, D7, D9: SFH 2701; LED-GULL
D2, D4, D6, D8: SFH 4059-QS; LED-GULL
IC1: MCP9701A; TO92
IC2: STM32F031K6T6; LQFP32-ST
IC3, IC4, IC5, IC6, IC7: OPA320; SOT23-5
IR: DF13-6P-1.25V; DF13C-6P-1.25V
IRRX: 009155003541006; AVX-CON3
IRTX: 009155003541006; AVX-CON3
L1: 120R; L0603
LED1: gr; CHIP-LED0603
PAD100, PAD101, PAD102, PAD103, PAD104, PAD105, PAD106, PAD107, PAD108, PAD109, PAD110, PAD111: WIREPADSMD1,4-3; SMD1,4-3
Q1: KC2016K4.00000C1GE00; OSCI-KC2016
Q2, Q3, Q4: DMN5L06DMK-7; SOT26
R1: 1k; R0603
R2, R3, R4, R5: 100; R0805
R6, R7, R8, R9, R10: 24; R0805
R11, R12, R13, R14, R15: 2M; R0603
SWCLK: WIREPADSMD1,27-254; SMD1,27-2,54
SWDIO: WIREPADSMD1,27-254; SMD1,27-2,54
X1, X2: 00-9155-006-741-006; AVX-CON6-2MM

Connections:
+3V3: C1.1, C3.1, C5.1, IC1.3 (+VS), IC2.1 (VDD), IC2.17 (VDD), IR.P$1 (1), IRRX.1, IRTX.1, L1.2, Q1.1 (OE), Q1.4 (VCC), R1.2, X1.1
BOOT5: IC2.31 (BOOT0), R5.1
GND: C1.2, C2.2, C3.2, C4.2, C5.2, IC1.1 (GND), IC2.16 (GND), IC2.32 (GND), IR.P$6 (6), IRRX.3, IRRX.S1, IRRX.S2, IRTX.S1, IRTX.S2, Q1.2 (GND), Q2.1 (S), Q2.4 (S), Q3.1 (S), Q3.4 (S), Q4.1 (S), Q4.2 (G), Q4.4 (S), X1.S1, X1.S2, X2.6, X2.S1, X2.S2
GNDA: C7.2, C9.2, C11.2, C13.2, C15.2, D1.A, D3.A, D5.A, D7.A, D9.A, IC3.2 (GND), IC3.3 (+IN), IC4.2 (GND), IC4.3 (+IN), IC5.2 (GND), IC5.3 (+IN), IC6.2 (GND), IC6.3 (+IN), IC7.2 (GND), IC7.3 (+IN), PAD106.1
IR0: IC2.30 (PB7), Q4.5 (G)
IR1: IC2.28 (PB5), Q3.5 (G)
IR2: IC2.29 (PB6), Q3.2 (G)
IR3: IC2.26 (PB3), Q2.5 (G)
IR4: IC2.27 (PB4), Q2.2 (G)
IR-ADC0: IC2.7 (PA1), IRRX.2
IR-ADC1: IC2.10 (PA4), X1.4
IR-ADC2: IC2.11 (PA5), X1.3
IR-ADC3: IC2.12 (PA6), X1.2
IR-ADC4: IC2.9 (PA3), X1.5
IR-ADC5: IC2.8 (PA2), X1.6
IR-L1: D2.C, PAD110.1
IR-L2: D4.C, PAD109.1
IR-L3: D6.C, PAD108.1
IR-L4: D8.C, PAD107.1
IR-LED: IC2.22 (PA12), LED1.C
IR-LED1: R10.2, X2.2
IR-LED2: R9.2, X2.3
IR-LED3: R8.2, X2.4
IR-LED4: R7.2, X2.5
IR-OUT1: C6.2, IC3.1 (OUT), PAD102.1, R11.2
IR-OUT2: C8.2, IC5.1 (OUT), PAD103.1, R12.2
IR-OUT3: C10.2, IC6.1 (OUT), PAD104.1, R13.2
IR-OUT4: C12.2, IC7.1 (OUT), PAD101.1, R14.2
IR-OUT5: C14.2, IC4.1 (OUT), PAD100.1, R15.2
unnamed: IR.P$4 (4), R4.2
unnamed: IC2.23 (PA13), SWDIO.1
unnamed: IR.P$5 (5), R5.2
unnamed: IC2.24 (PA14), SWCLK.1
unnamed: C14.1, D9.C, IC4.4 (-IN), R15.1
unnamed: C10.1, D5.C, IC6.4 (-IN), R13.1
unnamed: C8.1, D3.C, IC5.4 (-IN), R12.1
unnamed: Q3.3 (D), R10.1
unnamed: C6.1, D1.C, IC3.4 (-IN), R11.1
unnamed: IC2.2 (PF0-OSC_IN), Q1.3 (FO)
unnamed: C4.1, IC2.5 (VDDA), L1.1
unnamed: IRTX.3, R6.2
unnamed: C12.1, D7.C, IC7.4 (-IN), R14.1
unnamed: Q4.3 (D), R6.1
unnamed: Q3.6 (D), R9.1
unnamed: Q2.3 (D), R8.1
unnamed: Q2.6 (D), R7.1
unnamed: LED1.A, R1.1
SRST5: C2.1, IC2.4 (NRST), R4.1
T-ADC: IC1.2 (VO), IC2.6 (PA0)
UART5-RX: IR.P$2 (2), R2.2
UART5-TX: IR.P$3 (3), R3.2
USART1-RX: IC2.20 (PA10), R3.1
USART1-TX: IC2.19 (PA9), R2.1
VCCINT: C7.1, C9.1, C11.1, C13.1, C15.1, D2.A, D4.A, D6.A, D8.A, IC3.5 (VCC), IC4.5 (VCC), IC5.5 (VCC), IC6.5 (VCC), IC7.5 (VCC), PAD105.1

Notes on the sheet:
Design: A. Ryll



Board: 2 copper layers, 90.0 x 41.0 mm, 71 parts (12 on the bottom side), 54 nets.

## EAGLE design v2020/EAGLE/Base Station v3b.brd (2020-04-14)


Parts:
C1, C2, C3, C4, C5, C6, C7, C8, C11: 100n; C0603
C9, C10: 10u; C0603
IC1: 74LVC1G125DBV; SOT23-5
IC2: FT2232ST; LQFP48-ST
IC3: SC189-3.3; SOT23-5
IC4: 93C76B; SOT23-6
L1: 120R; 0603
L2: 2u2; IHLP1616
PWR: gr; CHIP-LED0603
Q1: CSTCR6M00G55-R0; CSTCR6M
R1, R6, R7: 1k; R0603
R2, R3: 33; R0603
R4: 1k5; R0603
R5: 1M; R0603
R8: 4k87; R0603
RN1: 10k; EXB28V
RN2, RN3: 100; EXB28V
USB1: USB-BU; USB-BMICRO

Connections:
+3V3: C3.1, C4.1, C5.1, C10.1, IC1.5 (VCC), IC2.10 (SI/WUA), IC2.14 (VCCIOA), IC2.26 (SI/WUB), IC2.31 (VCCIOB), IC3.4 (FB), L2.P$1 (1), R6.2, RN1.5 (2), RN1.7 (2), RN1.8 (2); also elsewhere on the board
+5V: C6.1, C7.1, C9.1, C11.1, IC2.3 (VCC1), IC2.4 (RESET), IC2.42 (VCC2), IC3.1 (VIN), IC3.3 (EN), IC4.6 (VCC), L1.2, R1.2, R8.2; also elsewhere on the board
GND: C1.2, C2.2, C3.2, C4.2, C5.2, C6.2, C7.2, C8.2, C9.2, C10.2, C11.2, IC1.3 (GND), IC2.9 (GND1), IC2.18 (GND2), IC2.25 (GND3), IC2.34 (GND4), IC2.45 (AGND), IC2.47 (TEST), IC3.2 (GND), IC4.2 (GND), PWR.C, Q1.2, RN1.6 (2), USB1.5 (GND); also elsewhere on the board
JTD-A2M1: IC1.2 (I), IC2.23 (ADBUS1), RN1.2 (1)
JTD-M2A1: IC2.22 (ADBUS2), RN2.4 (1)
unnamed: IC2.48 (EECS), IC4.5 (CS)
unnamed: IC2.1 (EESK), IC4.4 (CLK)
unnamed: IC2.2 (EEDATA), IC4.3 (DI), R7.2
unnamed: IC2.44 (XTOUT), Q1.3, R5.1
unnamed: IC4.1 (DO), R7.1, R8.1
unnamed: PWR.A, R6.1
unnamed: IC1.4 (O), RN2.1
unnamed: IC2.40 (BDBUS0), RN3.4 (1)
unnamed: IC2.39 (BDBUS1), RN3.1
unnamed: IC2.7 (USBDP), R3.2, R4.2
unnamed: IC2.8 (USBDM), R2.2
unnamed: IC2.5 (RSTOUT), R4.1
unnamed: C2.1, IC2.6 (3V3OUT)
unnamed: C8.1, L1.1, USB1.1 (VCC)
unnamed: R2.1, USB1.2 (D-)
unnamed: R3.1, USB1.3 (D+)
unnamed: C1.1, IC2.46 (AVCC), R1.1
unnamed: IC2.43 (XTIN), Q1.1, R5.2
SRST: IC2.15 (ACBUS0), RN1.4 (1); also elsewhere on the board
SW-OUT: IC3.5 (SW), L2.P$2 (2)
SWCLK: RN2.6 (2); also elsewhere on the board
SWCLK1: IC2.24 (ADBUS0), RN1.3 (1), RN2.3 (1)
SWDIO: RN2.5 (2), RN2.8 (2); also elsewhere on the board
SWDIO_OE: IC1.1 (OE), IC2.21 (ADBUS3), RN1.1
USART1_RX: RN3.5 (2); also elsewhere on the board
USART1_TX: RN3.8 (2); also elsewhere on the board

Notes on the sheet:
Power
Design: A. Ryll
USB
SWD+UART


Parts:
C12, C13: 3p; C0603
C14, C16, C19, C20, C21, C22, C23: 100n; C0603
C15, C17, C18: 10u; C0603
IC5: STM32F767VIT6; LQFP100-ST
IC6: CP11009; CP11009-THX
L3: 120R; 0603
LED1: rd; CHIP-LED0603
LED2: gr; CHIP-LED0603
Q2: ABS07W-32.768KHZ; CRYSTAL-07W
R9, R10: 1k; R0603
RESET1: BUTTON4
X1: 3034TR; CR2025

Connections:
25MHZ: IC5.12 (OSC_IN); also elsewhere on the board
+3V3: C16.1, C19.1, C20.1, C21.1, C22.1, C23.1, IC5.11 (VDD), IC5.20 (VREF+), IC5.21 (VDDA), IC5.27 (VDD), IC5.50 (VDD), IC5.75 (VDD), IC5.100 (VDD), L3.2, R9.2, R10.2; also elsewhere on the board
FMC_A16: IC5.58 (P11), IC6.4 (RS)
FMC_D0: IC5.61 (P14), IC6.21 (D0)
FMC_D1: IC5.62 (P15), IC6.22 (D1)
FMC_D2: IC5.81 (P0), IC6.23 (D2)
FMC_D3: IC5.82 (P1), IC6.24 (D3)
FMC_D4: IC5.37 (P7), IC6.25 (D4)
FMC_D5: IC5.38 (P8), IC6.26 (D5)
FMC_D6: IC5.39 (P9), IC6.27 (D6)
FMC_D7: IC5.40 (P10), IC6.28 (D7)
FMC_D8: IC5.41 (P11), IC6.7 (D8)
FMC_D9: IC5.42 (P12), IC6.8 (D9)
FMC_D10: IC5.43 (P13), IC6.9 (D10)
FMC_D11: IC5.44 (P14), IC6.10 (D11)
FMC_D12: IC5.45 (P15), IC6.11 (D12)
FMC_D13: IC5.55 (P8), IC6.12 (D13)
FMC_D14: IC5.56 (P9), IC6.13 (D14)
FMC_D15: IC5.57 (P10), IC6.14 (D15)
FMC_NE1: IC5.88 (P7), IC6.15 (CS)
FMC_NOE: IC5.85 (P4), IC6.6 (RD)
FMC_NWE: IC5.86 (P5), IC6.5 (WR)
GND: C12.2, C13.2, C14.2, C15.2, C16.2, C17.2, C18.2, C19.2, C20.2, C21.2, C22.2, C23.2, IC5.10 (GND), IC5.19 (VSSA), IC5.26 (GND), IC5.49 (GND), IC5.74 (GND), IC5.94 (BOOT0), IC5.99 (GND), IC6.1 (GND), RESET1.1, RESET1.2, X1.GND; also elsewhere on the board
JTAG_UNUSED1: IC5.77 (P15)
JTAG_UNUSED2: IC5.89 (P3)
LCD_ON: IC5.69 (P10), IC6.19 (LCD_ON)
LCD_RESET: IC5.68 (P9), IC6.17 (RESET)
LED0: IC5.28 (P4), LED2.C
LED1: IC5.29 (P5), LED1.C
MII_COL: IC5.25 (P3); also elsewhere on the board
MII_CRS: IC5.22 (P0); also elsewhere on the board
MII_INT: IC5.4 (P5); also elsewhere on the board
MII_MDC: IC5.16 (P1); also elsewhere on the board
MII_MDIO: IC5.24 (P2); also elsewhere on the board
MII_RXD0: IC5.32 (P4); also elsewhere on the board
MII_RXD1: IC5.33 (P5); also elsewhere on the board
MII_RXD2: IC5.34 (P0); also elsewhere on the board
MII_RXD3: IC5.35 (P1); also elsewhere on the board
MII_RX_CLK: IC5.23 (P1); also elsewhere on the board
MII_RX_DV: IC5.31 (P7); also elsewhere on the board
MII_RX_ER: IC5.46 (P10); also elsewhere on the board
MII_TXD0: IC5.51 (P12); also elsewhere on the board
MII_TXD1: IC5.52 (P13); also elsewhere on the board
MII_TXD2: IC5.17 (P2); also elsewhere on the board
MII_TXD3: IC5.95 (P8); also elsewhere on the board
MII_TX_CLK: IC5.18 (P3); also elsewhere on the board
MII_TX_EN: IC5.47 (P11); also elsewhere on the board
unnamed: C18.1, IC5.73 (VCAP)
unnamed: C17.1, IC5.48 (VCAP)
unnamed: LED2.A, R10.1
unnamed: LED1.A, R9.1
unnamed: C15.1, IC6.2 (VCC3.3), L3.1
OSC32_IN: C12.1, IC5.8 (P14), Q2.1
OSC32_OUT: C13.1, IC5.9 (P15), Q2.2
PHY_RESET: IC5.30 (P6); also elsewhere on the board
SPI2_MISO: IC5.53 (P14), IC6.33 (TP_DOUT)
SPI2_MOSI: IC5.54 (P15), IC6.31 (TP_DIN)
SPI2_SCK: IC5.71 (P12), IC6.29 (TP_CLK)
SPI3_MISO: IC5.79 (P11); also elsewhere on the board
SPI3_MOSI: IC5.80 (P12); also elsewhere on the board
SPI3_SCK: IC5.78 (P10); also elsewhere on the board
SRST: C14.1, IC5.14 (!RST), RESET1.3, RESET1.4; also elsewhere on the board
SWCLK: IC5.76 (P14); also elsewhere on the board
SWDIO: IC5.72 (P13); also elsewhere on the board
TP_CS: IC5.63 (P6), IC6.30 (TP_CS)
TP_IRQ: IC5.59 (P12), IC6.34 (TP_IRQ)
USART1_RX: IC5.93 (P7); also elsewhere on the board
USART1_TX: IC5.92 (P6); also elsewhere on the board
VBAT: IC5.6 (VBAT), X1.POS1, X1.POS2
WF1_BUSY: IC5.83 (P2); also elsewhere on the board
WF1_CS: IC5.87 (P6); also elsewhere on the board
WF1_IRQ: IC5.84 (P3); also elsewhere on the board
WF_ANT: IC5.5 (P6); also elsewhere on the board
WF_CPS: IC5.1 (P2); also elsewhere on the board
WF_CRX: IC5.3 (P4); also elsewhere on the board
WF_CTX: IC5.2 (P3); also elsewhere on the board
WF_ON: IC5.91 (P5); also elsewhere on the board

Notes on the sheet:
Main Processor
LCD
Design: A. Ryll


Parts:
100MBIT: gr; CHIP-LED0603
C24, C25, C26, C27, C28, C29, C30, C31: 100n; C0603
C32: 10u; C0603
ETH: SI-60062-F; RJ45-LED
IC7: DP83848CVV; LQFP48
Q3: 25MHz; 7X
R11, R12, R13: 1k; R0603
R14: 1k5; R0603
R15, R16: 2k2; R0603
R17: 4k87; R0603
RN4, RN5, RN6, RN8, RN9: 100; EXB28V
RN7: N/A; EXB28V

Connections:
25MHZ: IC7.25 (25MHZ_OUT); also elsewhere on the board
+3V3: C24.1, C25.1, C26.1, C27.1, C28.1, ETH.2 (TCT), ETH.5 (RCT), IC7.22 (AVDD33), IC7.32 (IOVDD33), IC7.48 (IOVDD33), Q3.1 (OE), Q3.4 (VCC), R11.2, R12.2, R13.2, R14.2, R15.2, R16.2, RN5.5 (2), RN5.6 (2), RN5.7 (2), RN5.8 (2), RN7.5 (2), RN7.6 (2), RN7.7 (2), RN7.8 (2); also elsewhere on the board
GND: C24.2, C25.2, C26.2, C27.2, C28.2, C29.2, C30.2, C31.2, C32.2, ETH.8 (CHSGND), ETH.9 (SHIELD), ETH.10 (SHIELD), IC7.15 (AGND), IC7.19 (AGND), IC7.35 (IOGND), IC7.36 (DGND), IC7.47 (IOGND), Q3.2 (GND), R17.1; also elsewhere on the board
MII_COL: RN8.2 (1); also elsewhere on the board
MII_CRS: RN9.4 (1); also elsewhere on the board
MII_INT: IC7.7 (PWR_DOWN/INT); also elsewhere on the board
MII_MDC: IC7.31 (MDC); also elsewhere on the board
MII_MDIO: IC7.30 (MDIO), R14.1; also elsewhere on the board
MII_RXD0: RN8.3 (1); also elsewhere on the board
MII_RXD1: RN8.4 (1); also elsewhere on the board
MII_RXD2: RN6.1; also elsewhere on the board
MII_RXD3: RN6.2 (1); also elsewhere on the board
MII_RX_CLK: RN9.2 (1); also elsewhere on the board
MII_RX_DV: RN9.3 (1); also elsewhere on the board
MII_RX_ER: RN8.1; also elsewhere on the board
MII_TXD0: RN4.1; also elsewhere on the board
MII_TXD1: RN4.2 (1); also elsewhere on the board
MII_TXD2: RN4.3 (1); also elsewhere on the board
MII_TXD3: RN4.4 (1); also elsewhere on the board
MII_TX_CLK: RN6.3 (1); also elsewhere on the board
MII_TX_EN: RN6.4 (1); also elsewhere on the board
unnamed: IC7.3 (TXD_0), RN4.8 (2)
unnamed: IC7.4 (TXD_1), RN4.7 (2)
unnamed: IC7.5 (TXD_2), RN4.6 (2)
unnamed: IC7.6 (TXD_3), RN4.5 (2)
unnamed: IC7.1 (TX_CLK), RN6.6 (2)
unnamed: IC7.2 (TX_EN), RN6.5 (2)
unnamed: IC7.45 (RXD_2), RN6.8 (2)
unnamed: IC7.46 (RXD_3), RN6.7 (2)
unnamed: IC7.43 (RXD_0), RN8.6 (2)
unnamed: IC7.44 (RXD_1), RN8.5 (2)
unnamed: IC7.42 (COL), RN8.7 (2)
unnamed: IC7.41 (RX_ER), RN8.8 (2)
unnamed: IC7.39 (RX_DV), RN9.6 (2)
unnamed: IC7.38 (RX_CLK), RN9.7 (2)
unnamed: IC7.40 (CRS/CRS_DV), RN9.5 (2)
unnamed: IC7.24 (RBIAS), R17.2
unnamed: C29.1, C30.1, C31.1, C32.1, IC7.18 (PFBIN1), IC7.23 (PFBOUT), IC7.37 (PFBIN2)
unnamed: IC7.20 (RESV), R15.1
unnamed: IC7.21 (RESV), R16.1
unnamed: ETH.12 (LED_YE-), IC7.26 (LED_ACT/COL), RN7.3 (1)
unnamed: 100MBIT.C, IC7.27 (LED_SPEED), RN7.2 (1)
unnamed: ETH.14 (LED_GR-), IC7.28 (LED_LINK), RN7.1
unnamed: ETH.6 (RD-), IC7.13 (RD-), RN5.4 (1)
unnamed: ETH.4 (RD+), IC7.14 (RD+), RN5.3 (1)
unnamed: ETH.3 (TD-), IC7.16 (TD-), RN5.2 (1)
unnamed: ETH.1 (TD+), IC7.17 (TD+), RN5.1
unnamed: 100MBIT.A, R11.1
unnamed: ETH.13 (LED_GR+), R12.1
unnamed: ETH.11 (LED_YE+), R13.1
unnamed: IC7.34 (X1), Q3.3 (FO)
PHY_RESET: IC7.29 (RESET_N); also elsewhere on the board

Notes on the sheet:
Design: A. Ryll
Ethernet PHY


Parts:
C33, C44: 0p5; C0402
C34, C36, C50, C52, C54: 100n; C0603
C35, C37, C51, C53, C55, C59, C60, C61, C62: 1n; C0603
C38: 100p; C0402
C39, C47: 47p; C0402
C40, C43, C48: NA; C0402
C41, C42: 1p2; C0402
C45: 1u; C0603
C46, C56: 10n; C0603
C49: 0p7; C0402
C57, C58: 10u; C0603
IC8: SKY66112; SMCM-22
IC9: SX1280; QFN24L
IC10: LP5907MFX-3.3; SOT23-5L
L4, L5: 120R; 0603
LED3: gr; CHIP-LED0603
Q4: FL520WFMT1; CRYSTAL-7M
R18, R21: 3n; R0402
R19, R20: 2n4; R0402
R22: 1k; R0603
RN10, RN11, RN12: 100; EXB28V
X2, X3: ANT-SMA-EDGERA; ANT-SMA-RA

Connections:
+5V: C58.1, IC10.1 (VIN); also elsewhere on the board
ANTS: C59.1, IC8.4 (ANT_SEL), RN12.8 (2)
CPS: C62.1, IC8.15 (CPS), RN12.6 (2)
CRX: C61.1, IC8.2 (CRX), RN12.7 (2)
CTX: C60.1, IC8.17 (CTX), RN12.5 (2)
GND: C34.2, C35.2, C36.2, C37.2, C40.2, C41.2, C42.2, C43.2, C44.2, C45.2, C46.2, C48.2, C49.2, C50.2, C51.2, C52.2, C53.2, C54.2, C55.2, C56.2, C57.2, C58.2, C59.2, C60.2, C61.2, C62.2, IC8.1 (GND), IC8.5 (GND), IC8.7 (GND), IC8.9 (GND), IC8.10 (GND), IC8.12 (GND), IC8.13 (GND), IC8.18 (GND), IC8.20 (GND), IC8.22 (GND), IC8.PAD1 (GND), IC8.PAD2 (GND), IC9.5 (GND), IC9.13 (GND), IC9.20 (GND), IC9.21 (GND), IC9.23 (GND), IC9.24 (GND), IC9.PAD (GND), IC10.2 (GND), LED3.C, Q4.2 (GND1), Q4.4 (GND2), X2.GND1 (GND), X2.GND2 (GND1), X2.GND3 (GND2), X2.GND4 (GND3), X3.GND1 (GND), X3.GND2 (GND1), X3.GND3 (GND2), X3.GND4 (GND3); also elsewhere on the board
unnamed: IC9.17 (MOSI), RN10.6 (2)
unnamed: IC9.16 (MISO), RN10.5 (2)
unnamed: IC9.18 (SCK), RN10.7 (2)
unnamed: IC9.19 (!CS), RN10.8 (2)
unnamed: IC9.7 (BUSY), RN11.8 (2)
unnamed: IC9.8 (DIO1), RN11.5 (2)
unnamed: LED3.A, R22.1
unnamed: IC9.6 (XTA), Q4.1
unnamed: IC9.4 (XTB), Q4.3 (2)
unnamed: C33.1, C41.1, R18.2, R19.1
unnamed: C33.2, C38.2, C42.1, R19.2
unnamed: C56.1, IC9.1 (VR_PA)
unnamed: C45.1, C46.1, IC9.2 (VDD_IN), IC9.12 (DCC_FB)
unnamed: C38.1, IC8.21 (RFIN)
unnamed: C39.2, C43.1, R20.1
unnamed: C44.1, R20.2, X2.C (1)
unnamed: C47.2, C48.1, R21.1
unnamed: C49.1, R21.2, X3.C (1)
unnamed: C39.1, IC8.8 (ANT1)
unnamed: C47.1, IC8.6 (ANT2)
RFIO1: C40.1, IC9.22 (RFIO), R18.1
SPI3_MISO: RN10.4 (1); also elsewhere on the board
SPI3_MOSI: RN10.3 (1); also elsewhere on the board
SPI3_SCK: RN10.2 (1); also elsewhere on the board
WF1_BUSY: RN11.1; also elsewhere on the board
WF1_CS: RN10.1; also elsewhere on the board
WF1_IRQ: RN11.4 (1); also elsewhere on the board
WF_3V3: C57.1, IC10.5 (VOUT), L4.1, L5.1, R22.2
WF_3V3FEM: C50.1, C51.1, C52.1, C53.1, C54.1, C55.1, IC8.3 (CSD), IC8.11 (VDD), IC8.14 (VCC2), IC8.16 (VCC1), IC8.19 (CHL), L5.2
WF_3V3SX: C34.1, C35.1, C36.1, C37.1, IC9.3 (!RESET), IC9.11 (V_DIO), IC9.15 (VBAT), L4.2
WF_ANT: RN12.1; also elsewhere on the board
WF_CPS: RN12.3 (1); also elsewhere on the board
WF_CRX: RN12.2 (1); also elsewhere on the board
WF_CTX: RN12.4 (1); also elsewhere on the board
WF_ON: IC10.3 (ON); also elsewhere on the board

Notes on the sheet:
Design: A. Ryll
Wireless Interface

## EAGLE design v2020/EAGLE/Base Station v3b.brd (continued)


Board: 4 copper layers, 58.0 x 85.0 mm, 127 parts (0 on the bottom side), 157 nets.

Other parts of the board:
U$1: BMI-S-204-F; SHIELD-32MM

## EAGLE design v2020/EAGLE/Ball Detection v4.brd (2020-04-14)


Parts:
C1: 10p; C0603
C2: 10u; C0603
D1: VSMB2000X01; LED-GULLR
D2: TEMD1000; LED-GULLR
IC1: OPA320; SOT23-5
R1: 1M; R0603

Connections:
GND: C2.1, D2.A, IC1.2 (GND), IC1.3 (+IN)
IR-ADC: C1.2, IC1.1 (OUT), R1.2
unnamed: C1.1, D2.C, IC1.4 (-IN), R1.1
RX+3V3: C2.2, IC1.5 (VCC)
TX+3V3: D1.A
TX-LED: D1.C

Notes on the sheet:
Design: A. Ryll



Board: 2 copper layers, 10.0 x 51.0 mm, 6 parts (5 on the bottom side), 4 nets.

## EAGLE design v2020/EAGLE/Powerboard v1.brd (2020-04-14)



Board: 4 copper layers, 90.0 x 80.0 mm, 372 parts (4 on the bottom side), 363 nets.

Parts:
CON:C15: 100n; C0603
CON:EXT: DF13-8P-1.25V; DF13C-8P-1.25V
CON:IC1: TCA9539RTW; WQFN24
CON:IR: DF13-6P-1.25V; DF13C-6P-1.25V
CON:KD: DF13-12P-1.25V; DF13C-12P-1.25V
CON:PAD1, CON:PAD2, CON:PAD3: 5,4/3,0
CON:PAD4: 9774030243R; 5,4/3,0
CON:Q8: BSS84; SOT23
CON:Q17: BSS138; SOT23
CON:R1, CON:R12: 1k33 1%; R0603
CON:R40: 5k6; R0603
CON:RN1, CON:RN2, CON:RN9: 10k; EXB28V
CON:RN7, CON:RN8: 100; EXB28V
CON:SG1: CEM-1212S; F/QMX
CON:X1: 4-1734742-0; TE-4-1734742-0
DEBUG:C16, DEBUG:C17, DEBUG:C34, DEBUG:C35, DEBUG:C36, DEBUG:C37, DEBUG:C38: 100n; C0603
DEBUG:IC8: 74LVC1G125DBV; SOT23-5
DEBUG:IC9: 93C76B; SOT23-6
DEBUG:IC10: FT2232ST; LQFP48-ST
DEBUG:L3: 120R; L0603
DEBUG:Q4: CSTCR6M00G55-R0; CSTCR6M
DEBUG:R12, DEBUG:R26: 1k; R0603
DEBUG:R13: 5k6; R0603
DEBUG:R14: 1M; R0603
DEBUG:R15, DEBUG:R24: 33; R0603
DEBUG:R25: 1k33 1%; R0603
DEBUG:RN3: 10k; EXB28V
DEBUG:RN4, DEBUG:RN5: 100; EXB28V
DEBUG:S1: USB-BU; USB-BMICRO
DRIBBLER:C1, DRIBBLER:C2, DRIBBLER:C3, DRIBBLER:C4, DRIBBLER:C12, DRIBBLER:C23, DRIBBLER:C25, DRIBBLER:C26: 100n; C0603
DRIBBLER:C5, DRIBBLER:C6, DRIBBLER:C7, DRIBBLER:C8, DRIBBLER:C9, DRIBBLER:C10, DRIBBLER:C11, DRIBBLER:C13, DRIBBLER:C14, DRIBBLER:C157: 10u; C1206
DRIBBLER:C21: 47p; C0603
DRIBBLER:C22, DRIBBLER:C24, DRIBBLER:C27: 1u; C0603
DRIBBLER:IC1: STSPIN32F0A; VFQFPN48
DRIBBLER:IC6: SN74LVC3G17DCT; DCT_R-PDSO-G8
DRIBBLER:L1, DRIBBLER:L6: 120R; L0603
DRIBBLER:LED2: gr; CHIP-LED0603
DRIBBLER:Q1, DRIBBLER:Q2, DRIBBLER:Q3: FDMD85100; POWER56_HBRIDGE
DRIBBLER:Q5: KC2016K4.00000C1GE00; OSCI-KC2016
DRIBBLER:R1, DRIBBLER:R2, DRIBBLER:R3, DRIBBLER:R4, DRIBBLER:R5, DRIBBLER:R6: 33; R0603
DRIBBLER:R9: 1k; R0603
DRIBBLER:R16: 0R025; R1206
DRIBBLER:R17, DRIBBLER:R18: 1k33 1%; R0603
DRIBBLER:R19: 7k32 1%; R0603
DRIBBLER:R20: 16k2 1%; R0603
DRIBBLER:R22: 243k 1%; R0603
DRIBBLER:R23: 24k 1%; R0603
DRIBBLER:RN1, DRIBBLER:RN6: 100; EXB28V
DRIBBLER:SWCLK: TPTP10R; TP10R
DRIBBLER:SWDIO: TPTP10R; TP10R
DRIBBLER:X1: 640454-8
MOTOR1:C1, MOTOR1:C2, MOTOR1:C3, MOTOR1:C4, MOTOR1:C5, MOTOR1:C12, MOTOR1:C23, MOTOR1:C25, MOTOR1:C26, MOTOR2:C1, MOTOR2:C2, MOTOR2:C3, MOTOR2:C4, MOTOR2:C5, MOTOR2:C12, MOTOR2:C23, MOTOR2:C25, MOTOR2:C26, MOTOR3:C1, MOTOR3:C2, MOTOR3:C3, MOTOR3:C4, MOTOR3:C5, MOTOR3:C12, MOTOR3:C23, MOTOR3:C25, MOTOR3:C26, MOTOR4:C1, MOTOR4:C2, MOTOR4:C3, MOTOR4:C4, MOTOR4:C5, MOTOR4:C12, MOTOR4:C23, MOTOR4:C25, MOTOR4:C26: 100n; C0603
MOTOR1:C6, MOTOR1:C7, MOTOR1:C8, MOTOR1:C9, MOTOR1:C10, MOTOR1:C11, MOTOR1:C13, MOTOR1:C14, MOTOR1:C15, MOTOR1:C157, MOTOR2:C6, MOTOR2:C7, MOTOR2:C8, MOTOR2:C9, MOTOR2:C10, MOTOR2:C11, MOTOR2:C13, MOTOR2:C14, MOTOR2:C15, MOTOR2:C157, MOTOR3:C6, MOTOR3:C7, MOTOR3:C8, MOTOR3:C9, MOTOR3:C10, MOTOR3:C11, MOTOR3:C13, MOTOR3:C14, MOTOR3:C15, MOTOR3:C157, MOTOR4:C6, MOTOR4:C7, MOTOR4:C8, MOTOR4:C9, MOTOR4:C10, MOTOR4:C11, MOTOR4:C13, MOTOR4:C14, MOTOR4:C15, MOTOR4:C157: 10u; C1206
MOTOR1:C16, MOTOR2:C16, MOTOR3:C16, MOTOR4:C16: 470u; C22-12.5L
MOTOR1:C21, MOTOR2:C21, MOTOR3:C21, MOTOR4:C21: 47p; C0603
MOTOR1:C22, MOTOR1:C24, MOTOR1:C27, MOTOR2:C22, MOTOR2:C24, MOTOR2:C27, MOTOR3:C22, MOTOR3:C24, MOTOR3:C27, MOTOR4:C22, MOTOR4:C24, MOTOR4:C27: 1u; C0603
MOTOR1:IC1, MOTOR2:IC1, MOTOR3:IC1, MOTOR4:IC1: STSPIN32F0A; VFQFPN48
MOTOR1:IC6, MOTOR1:IC11, MOTOR2:IC6, MOTOR2:IC11, MOTOR3:IC6, MOTOR3:IC11, MOTOR4:IC6, MOTOR4:IC11: SN74LVC3G17DCT; DCT_R-PDSO-G8
MOTOR1:L1, MOTOR1:L6, MOTOR2:L1, MOTOR2:L6, MOTOR3:L1, MOTOR3:L6, MOTOR4:L1, MOTOR4:L6: 120R; L0603
MOTOR1:LED2, MOTOR2:LED2, MOTOR3:LED2, MOTOR4:LED2: gr; CHIP-LED0603
MOTOR1:Q1, MOTOR1:Q2, MOTOR1:Q3, MOTOR2:Q1, MOTOR2:Q2, MOTOR2:Q3, MOTOR3:Q1, MOTOR3:Q2, MOTOR3:Q3, MOTOR4:Q1, MOTOR4:Q2, MOTOR4:Q3: FDMD85100; POWER56_HBRIDGE
MOTOR1:Q5, MOTOR2:Q5, MOTOR3:Q5, MOTOR4:Q5: KC2016K4.00000C1GE00; OSCI-KC2016
MOTOR1:R1, MOTOR1:R2, MOTOR1:R3, MOTOR1:R4, MOTOR1:R5, MOTOR1:R6, MOTOR2:R1, MOTOR2:R2, MOTOR2:R3, MOTOR2:R4, MOTOR2:R5, MOTOR2:R6, MOTOR3:R1, MOTOR3:R2, MOTOR3:R3, MOTOR3:R4, MOTOR3:R5, MOTOR3:R6, MOTOR4:R1, MOTOR4:R2, MOTOR4:R3, MOTOR4:R4, MOTOR4:R5, MOTOR4:R6: 33; R0603
MOTOR1:R9, MOTOR2:R9, MOTOR3:R9, MOTOR4:R9: 1k; R0603
MOTOR1:R16, MOTOR2:R16, MOTOR3:R16, MOTOR4:R16: 0R025; R1206
MOTOR1:R17, MOTOR1:R18, MOTOR2:R17, MOTOR2:R18, MOTOR3:R17, MOTOR3:R18, MOTOR4:R17, MOTOR4:R18: 1k33 1%; R0603
MOTOR1:R19, MOTOR2:R19, MOTOR3:R19, MOTOR4:R19: 7k32 1%; R0603
MOTOR1:R20, MOTOR2:R20, MOTOR3:R20, MOTOR4:R20: 16k2 1%; R0603
MOTOR1:R22, MOTOR2:R22, MOTOR3:R22, MOTOR4:R22: 243k 1%; R0603
MOTOR1:R23, MOTOR2:R23, MOTOR3:R23, MOTOR4:R23: 24k 1%; R0603
MOTOR1:RN1, MOTOR1:RN2, MOTOR1:RN6, MOTOR2:RN1, MOTOR2:RN2, MOTOR2:RN6, MOTOR3:RN1, MOTOR3:RN2, MOTOR3:RN6, MOTOR4:RN1, MOTOR4:RN2, MOTOR4:RN6: 100; EXB28V
MOTOR1:SWCLK, MOTOR1:SWDIO, MOTOR2:SWCLK, MOTOR2:SWDIO, MOTOR3:SWCLK, MOTOR3:SWDIO, MOTOR4:SWCLK, MOTOR4:SWDIO: TPTP10R; TP10R
MOTOR1:X2, MOTOR2:X2, MOTOR3:X2, MOTOR4:X2: 1-640454-2
POWER:BAT+: 5,08/3
POWER:BAT-: 5,08/3
POWER:C53, POWER:C54, POWER:C55, POWER:C56, POWER:C58, POWER:C67, POWER:C68, POWER:C69, POWER:C73, POWER:C75, POWER:C80: 100n; C0603
POWER:C57: 10n; C0603
POWER:C59, POWER:C71: 1u; C0603
POWER:C60, POWER:C64: 18p; C0603
POWER:C61, POWER:C65, POWER:C74, POWER:C76, POWER:C77, POWER:C78, POWER:C79: 33u; C1206
POWER:C62, POWER:C63, POWER:C66, POWER:C70, POWER:C72: 10u; C1206
POWER:IC14: LTC2955CTS8-1; SOT23-8
POWER:IC16: LTC4231CMS-2; MSOP-12
POWER:IC17: INA226; DGS_S-PDSO-G10
POWER:IC18, POWER:IC19: LMR23630ADDA; DDA_R-PDSO-G8
POWER:IC20: LTC4415MSE; MSOP-16P
POWER:IC21: LT3080ST; SOT223
POWER:L8, POWER:L9: 7443251600; WE-HCI
POWER:L10, POWER:L11, POWER:L12: 470R; L1206
POWER:L13: 120R; L0603
POWER:LED1: gr; CHIP-LED0603
POWER:Q7: FDD86367; D-PAK_TO252AA
POWER:R11: 5k6; R0603
POWER:R27: 40k2 1%; R0603
POWER:R28: 24k 1%; R0603
POWER:R31, POWER:R42: 1M; R0603
POWER:R41: 7k32 1%; R0603
POWER:R43, POWER:R55: 1k; R0603
POWER:R44: 0R001; R2512
POWER:R46: 0R002; R2512
POWER:R48: 243k 1%; R0603
POWER:R49, POWER:R51, POWER:R52: 22k1 1%; R0603
POWER:R50, POWER:R53: 88k7 1%; R0603
POWER:R54: 330k; R0603
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

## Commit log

2020-04-14 Release files for v2020 electronics
    [Ball Detection v4 Panel.brd, Ball Detection v4.brd, Ball Detection v4.sch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]
2025-07-08 Added project files for KiCad9 converted from EAGLE
    [Ball Detection v4.kicad_pcb, Ball Detection v4.kicad_sch, Base Station v3b.kicad_pcb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]

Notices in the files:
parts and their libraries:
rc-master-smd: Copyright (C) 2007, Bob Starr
